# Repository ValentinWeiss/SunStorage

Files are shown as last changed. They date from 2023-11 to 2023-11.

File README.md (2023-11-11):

# SunStorage

## Installation

### Prerequisites

Install CP210x Windows Drivers: https://www.silabs.com/developers/usb-to-uart-bridge-vcp-drivers?tab=downloads

### PlatformIO
- Install the PlatformIO extension in VS Code
- Open the SunStorage project in VS Code and open the PlatformIO tab in the side menu
- Wait until PlaformIO has installed all dependencies for the SunStorage project

## Using ESP-IDF

### Tasks
Create a task for each application. To do that you have to follow the following steps:

1. Declare your application main function (choose a speaking name, not "main")
2. Add a corresponding function call of ```xTaskCreate``` to the ```app_main``` function in the file ```main.c```. The pcName can only be an array up to 16 bytes and for the stack size use a number as small as possible.<br/>
(read the Documentation for detailed information: https://docs.espressif.com/projects/esp-idf/en/latest/esp32/api-reference/system/freertos_idf.html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)
2. Only create those tasks in ```app_main``` function that you want to run continuously, because the ```app_main``` function will return when all the tasks have been created. Therefore do not use the returned handle and do not create a task with parameters there!!!

## Compiling

Compile flags can be set in the platformio.ini file.

-DTX: compile code for ESP1 (TX)

-DRX: compile code for ESP2 (RX)

## Flashing

PlatformIO: -> Press Build -> Press Upload and Monitor -> While "Connecting..." press BOOT Button then EN Button on the ESP board. https://docs.espressif.com/projects/esp-idf/en/latest/esp32/hw-reference/esp32/get-started-devkitc.html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

## Ports
If you want to reserve a port add it to the Dokumentation\Architektur\Pinout.md file.

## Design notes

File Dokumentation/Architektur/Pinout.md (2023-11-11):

## PORTS

Some of the listed ports are not available in general since they have a fixed purpose. (e.g. power supply)

# ESP 1 (TX)

GPIO 0: strange outputs during startup

GPIO 1: GPS_GPIO_TX

GPIO 2: High Power Circuit Enable

GPIO 3: GPS_GPIO_RX

GPIO 4:

GPIO 5: SD MISO

GPIO 6: Used for internal flash

GPIO 7: Used for internal flash

GPIO 8: Used for internal flash

GPIO 9: Used for internal flash

GPIO 10: Used for internal flash

GPIO 11: Used for internal flash

GPIO 12: Cell Balancing Lower Cell

GPIO 13: Coulomb Counter Discharge

GPIO 14: Cell Balancing Higher Cell

GPIO 15: DCF77 Signal

GPIO 16: UART ESP2 RX

GPIO 17: UART ESP2 TX

GPIO 18: SD MOSI

GPIO 19: SD CLK

GPIO 20: Does not exist

GPIO 21: I2C_MASTER_SDA_IO

GPIO 22: I2C_MASTER_SCL_IO

GPIO 23: SD CS

GPIO 24: Does not exist

GPIO 25: DAC USB Charger Mode 0

GPIO 26: DAC USB Charger Mode 1

GPIO 27: PWM Solar Charger

GPIO 28: Does not exist

GPIO 29: Does not exist

GPIO 30: Does not exist

GPIO 31: Does not exist

GPIO 32: ADC Battery Voltage

GPIO 33: ADC Solar Current

GPIO 34: ADC System Current

GPIO 35: ADC Battery Cell 0 Voltage

GPIO 36 (SP):

GPIO 39 (SN): ADC Coulomb

# ESP 2 (RX)

GPIO 0: strange outputs during startup

GPIO 1:

GPIO 2: Button 0

GPIO 3:

GPIO 4: Servo Rotate

GPIO 5: Servo Tilt

GPIO 6: Used for internal flash

GPIO 7: Used for internal flash

GPIO 8: Used for internal flash

GPIO 9: Used for internal flash

GPIO 10: Used for internal flash

GPIO 11: Used for internal flash

GPIO 12:

GPIO 13: LCD ON/OFF

GPIO 14:

GPIO 15: LCD D6

GPIO 16: UART ESP 1 RX

GPIO 17: UART ESP 1 TX

GPIO 18: LCD E

GPIO 19: LCD RS

GPIO 20: Does not exist

GPIO 21:

GPIO 22:

GPIO 23:

GPIO 24: Does not exist

GPIO 25: LCD D4

GPIO 26: LCD D7

GPIO 27: LCD D5

GPIO 28: Does not exist

GPIO 29: Does not exist

GPIO 30: Does not exist

GPIO 31: Does not exist

GPIO 32:

GPIO 33:

GPIO 34:

GPIO 35:

GPIO 36: Button 1

GPIO 39:

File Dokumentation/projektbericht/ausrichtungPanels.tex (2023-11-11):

\chapterauthor{Felix Wagner}
Die Ausrichtung der Solarpanele erfolgt über die vom Haupt-ESP berechneten Azimut und Elevation Werte.
Diese repräsentieren die Position der Sonne am Himmel. 
Wenn davon ausgegangen wird, dass der SunStorage Aufbau stets auf einer ebenen Fläche liegt, dann können die Azimut- und Elevationwerte direkt auf die Postionen der Rotations- und Kippservos übertragen werden. 
Somit würde sich eine direkte Ausrichtung zur Sonne ergeben und die Effektivität der Solarpanele wäre maximiert.
Dieser Fall ist jedoch im praktischen Betrieb nicht immer gegeben.

\subsubsection{Schieflage des Systems}
Steht der Aufbau schief, so ist die Trennung der Aufgabengebiete des Rotieren und Kippens der Solarpanele nicht mehr gegeben.
Somit können die Azimut und Elevation nicht mehr direkt für die Stellung der Servomotoren verwendet werden.
Kippt man etwa den kompletten Aufbau auf eine Seite, so sind die Aufgaben der Motoren komplett umgekehrt.
Für alle Orientierungen dazwischen übernehmen die Motoren Rotation und Kippen gemeinsam.

\paragraph{Beschleunigungswerte}
Um die Lage des SunStorage Systems zu ermitteln, muss die Erdbeschleunigung anhand von drei Achsen gemessen werden. 
Dies erfolgt über die Daten des Beschleunigungssensors.

\paragraph{Interpretation der Beschleunigungswerte}
Betrachtet man die Beschleunigungswerte der drei Achsen als Vektor im 3-dimensionalen Raum, 
so spannt dieser Vektor eine Ebene auf. 
Dieser Vektor muss nun an der z-Achse im Koordinatensystem gespiegelt werden. 
Damit lässt sich die physikalische Lage von SunStorage im Koordinatensystem abbilden.
Dieser Vektor wird im weiteren Verlauf $ V_{SunStorage} $ genannt.

\paragraph{Darstellen der Sonne im Koordinatensystem}
Nachdem nun SunStorage im Koordinatensystem abgebildet ist, muss die gewünschte Sonnenposition mittels eines Vektors hinzugefügt werden.
Wie bereits bekannt wird die Sonnenposition über die Werte Azimut und Elevation angegeben. 
Dabei handelt es sich um Winkel. 
Diese können mithilfe der trigonometrischen Funktionen in einem 3-dimensionalen Vektor übersetzt werden.
Hierfür wird die Berechnung in vier verschiedene Fälle aufgeteilt, welche die vier Quadranten eines 2-dimensionalen Koordinatensystems darstellen. 
\begin{itemize}
    \item I Quadrant: $x = 1 y = \tan(Azimuth)$
    \item II Quadrant: $x = -1 y = -\tan(Azimuth)$
    \item III Quadrant: $x = -1 y = -\tan(Azimuth)$
    \item IV Quadrant: $x = -\tan(Azimuth) y = -1$
\end{itemize}
Anschließend wird der Vektor aus dem Punkt (x,y) und dem Ursprung normalisiert, um mit dem später berechneten z-Wert die Sonnenposition darzustellen.\\
Die z-Koordinate wird anschließend über den Tangens des Elevationwertes bestimmt. 

$$ z = \tan(Elevation) $$

Nun stellen x, y und z den Sonnenvektor $ V_{Sonne} $ dar.\\
Ist der Elevationswinkel 90°, so wird $ V_{Sonne} $ auf (0,0,1) gesetzt, da in diesem Fall der Azimutwert vernachlässigbar ist.
Nun kann die Sonnenposition im Koordinatensystem dargestellt werden.

\paragraph{Solarpanele darstellen}
Um die Orientierung der Solarpanele im Koordinatensystem darzustellen, wird eine Ebene konstruiert, welche die Panele senkrecht in ihrer Mitte trennt.
Diese wird über die Berechnung des Orthogonalvektors der z-Achse und $ V_{SunStorage} $ bestimmt:
\[
\begin{pmatrix}
    0\\
    0\\
    1\\
\end{pmatrix}
\times
V_{SunStorage}
=
V_{ortho}
\]
Aus dem Vektor $ V_{ortho} $ lässt sich die Koordinatenform als Ebene erstellen.
\[V_{ortho}x \cdot x + V_{ortho}y \cdot y + V_{ortho}z \cdot z = 0\] 
Nun kann diese Ebene um die Achse von $ V_{SunStorage} $ rotiert werden.
Dies wird über die allgemeine Drehmatrix umgesetzt.
\[
R_n(\alpha)
=
\begin{pmatrix}
    n^2_1(1-\cos\alpha)+\cos\alpha & n_1n_2(1-\cos \alpha)-n_3\sin\alpha & n_1n_3(1-\cos\alpha)+n_2\sin\alpha\\
    n_2n_1(1-\cos\alpha)+n_3\sin\alpha & n^2_2(1-\cos\alpha)+\cos\alpha & n_2n_3(1-\cos\alpha)-n_1\sin\alpha\\
    n_3n_1(1-\cos\alpha)-n_2\sin\alpha & n_3n_2(1-\cos\alpha)+n_1\sin\alpha & n^2_3(1-\cos\alpha)+\cos\alpha\\
\end{pmatrix}    
\]
An Stelle von $ n = (n_1, n_2, n_3)^T $ wird $ V_{SunStorage}^T $ eingesetzt.
Dies entspricht der Bewegung des Rotationsservomotors.
Anschließend kann die Rotation der Ebene gesucht werden, für die $ V_{Sonne} $ eingesetzt
in  die Koordinatenform der Ebene des Normalenvektors $ V_{ortho} $ den geringsten Wert hat. %TODO der satz doof
Damit ist die Bestimmung der Stellung des Rotationsmotors beendet, da dies bedeutet, 
dass $ V_{Sonne} $ in der Ebene von  $ V_{ortho} $ liegt.
Anschließend erfolgt die Berechnung der Stellung des Kippmotors.
Dafür wird ein weiterer Orthogonalvektor $ V_{opt} $ erzeugt. 
Dieser liegt zwischen der z-Achse und $ V_{ortho} $. 
Die Stellung des Kippmotors kann somit durch die Berechnung des Winkels zwischen $ V_{opt} $ und $ V_{Sonne} $ bestimmt werden:
\[\alpha = \arccos(\frac{V_{opt} \cdot V_{Sonne}}{\left| V_{opt} \right| \cdot \left| V_{Sonne} \right|})\]

\subsubsection{Schieflage des Kompass}
Der Kompass liefert in Abhängigkeit seiner Ausrichtung unterschiedliche Werte.
In diesem Kapitel wird die notwendige Korrektur beschrieben.
\paragraph{Nordausrichtung}
\chapterauthor{Felix Wagner}
Die Bestimmung der Orientierung zu Norden erfolgt über die Winkelberechnung zwischen der 
y-Achse und der Geraden des Koordinatenursprungs und des aktuellen (x, y)-Messpunkts. 
Dieser Winkel wird mittels der Tangensfunktion ermittelt. Siehe Abbildung \autoref{fig:circlecenter}.
Die C Standardbibiliothek $math.h$ liefert hierfür die Funktion $atan2f$, 
welche den Winkel als float Datentyp zurückgibt 
und die vier verschiedenen Quadranten des Koordinatensystems berücksichtigt.

\paragraph{Schieflagenkorrektur}
\chapterauthor{Felix Wagner}
Es ist nicht immer gegeben, dass der Kompass perfekt gerade liegt. 
Deshalb müssen die Sensorwerte unter Berücksichtigung des vom Beschleunigungssensor 
gestelltem Orientierungsvektor angepasst werden. 
Dies erfolgt über die sogenannte Vektorprojektion. 
Dabei wird über folgende Formel \[\vec{a_{projected}} = \frac{\vec{a} \circ \vec{b}}{\vec{b} \circ \vec{b}} \cdot \vec{b} \]
der Vektor aus den Kompasswerten auf die Orientierung des Vektors der Beschleunigungswerte projeziert. 
Anschließend werden die x- und y-Werte des projezierten Vektors von denen des Kompassvektors subtrahiert. 
Somit sind die Kompasswerte bereit für die oben besprochene Weiterverarbeitung.

\subsubsection{Verbesserter Algorithmus}
Der implementierte Algorithmus nutzt für seine Berechnung viele Multiplikationen und trigonometrische Funktionen.
Dies erzeugt einen großen Rechenaufwand und ist im Dauerbetrieb nicht optimal.
Dies wirkt sich aufgrund der großen zeitlichen Abstände der Funktionsaufrufe kaum negativ auf die Funktionsweise von SunStorage aus.
Im Folgenden wird eine effizientere Formel erklärt.\\
Die Berechnung von $ V_{SunStorage} $  und $ V_{Sonne} $ erfolgt analog zum ursprünglichen Algorithmus.
Anstatt einer Ebene für die Solarpanele eine Ebene über den Vektor $ V_{SunStorage} $ in Koordinatenform erzeugt.
\[V_{SunStorage}x \cdot x + V_{SunStorage}y \cdot y + V_{SunStorage}z \cdot z = 0\] 
Anschließend wird die Spitze von $ V_{Sonne} $ als Ausgangspunkt für eine Gerade $ G_{Sonne} $ mit dem Richtungsvektor $ V_{SunStorage} $ generiert.
Der Schnittpunkt von $ G_{Sonne} $ mit der Ebene von SunStorage stellt mit dem Ursprung des Koordinatensystems den Vektor $ V_{opt} $ dar.
Aus $ V_{opt} $ kann wiederum die Stellung für Rotation und Kippen der Motoren analog zum vorherigen Ansatz berechnet werden.

\subsubsection{Bestimmung der Abweichung zum Norden}
\chapterauthor{Felix Wagner}
Die Bestimmung der Orientierung zu Norden erfolgt über die Winkelberechnung zwischen der 
y-Achse, der Geraden des Koordinatenursprungs und des aktuellen (x, y)-Messpunkts. 
Dieser Winkel wird mittels der Tangensfunktion ermittelt. (siehe \autoref{fig:circlecenter})
Die C Standardbibliothek $math.h$ liefert hierfür die Funktion $atan2f$, 
welche den Winkel als float Datentyp zurückgibt und dabei die vier verschiedenen Quadranten des Koordinatensystems berücksichtigt.

\paragraph{Schieflagenkorrektur}
Es ist nicht immer gegeben, dass der Kompass perfekt gerade liegt. 
Deshalb müssen die Sensorwerte unter Berücksichtigung des Orientierungsvektors, die der Beschleunigungssensor liefert, angepasst werden. 
Dies erfolgt über eine Vektorprojektion.
Mithilfe der folgenden Formel wird der Vektor aus den Kompasswerten auf die Orientierung des Vektors der Beschleunigungswerte projiziert.
\[\vec{a_{projected}} = \frac{\vec{a} \circ \vec{b}}{\vec{b} \circ \vec{b}} \cdot \vec{b} \]
 
Anschließend werden die x- und y-Werte des projizierten Vektors von den Werten des Kompassvektors subtrahiert. 
Somit sind die Kompasswerte bereit für die in Weiterverarbeitung. \autocite{compasstilt}

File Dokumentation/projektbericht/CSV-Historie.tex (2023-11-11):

\subsubsection{CSV-Historie}\label{csvhistory}
\chapterauthor{Johannes Treske}
Eine Historie der Messdaten wird benötigt, um eine grafische Darstellung über die Zeit, im Web-Frontend darzustellen.
Ursprünglich war geplant, eine SQLite Datenbank zu verwenden.
Diese sollte auf der SD-Karte gespeichert werden.
Es gibt jedoch nur SQLite Bibliotheken, die mit älteren Versionen von ESP-IDF kompatibel sind, welche aber von unserem Modell des ESP32 nicht unterstützt werden.
Deswegen nutzen wir CSV-Dateien zum Speichern der Messdaten.

Für jeden Tag wird eine eigene CSV-Datei verwendet, die nach einem Teil des Timestamps benannt wird (YYYYMMDD.csv).
Innerhalb einer Datei besteht eine Zeile immer aus einer Reihe an Messdaten, eindeutig bestimmbar durch den Timestamp und getrennt durch Kommas.
Eine Zeile besteht aus allen Messwerten, die im Datenbankmodell in \autoref{fig. Datenbankmodell} zu sehen sind.
Um eine einfache Interaktion mit der Datenbank zu ermöglichen, wurde das Datenbankinterface geschrieben.
Die zwei wichtigsten Funktionen ermöglichen das Schreiben eines Messdatensets bzw. das Auslesen von Messdaten.

\begin{lstlisting}[language=C]
esp_err_t dbStoreReadings(readings_data_set_t readings);
esp_err_t dbGetReadings(readings_read_config_t config, cJSON** jsonOut);
\end{lstlisting}

Die Funktionsdeklaration der Lese-Funktion zeigt, dass ein JSON-Objekt zurückgegeben wird.
Dieses Objekt besteht aus einem JSON-Array, der alle Messdaten der gewünschten Zeitspanne, in Sets zusammengefasst, enthält.
Das JSON-Objekt kann so direkt an das Web-Frontend weitergegeben werden.
Über den \textit{config} Parameter kann eingestellt werden, welcher Zeitbereich abgefragt werden soll und welche Spalten/Messdaten benötigt werden.

Bei allen Funktionen des Datenbankinterfaces muss stets darauf geachtet werden, dass nicht mehrere Tasks auf die gleiche Datei zugreifen können.
Dieses Problem wird durch das Verwenden von Mutexen gelöst.
Weitere Funktionen, die das Datenbankinterface bereitstellt, sind Funktionen zum Initialisieren bzw. Deinitialisieren, sowie Funktionen, mit denen Daten gelöscht werden können.

\begin{figure}
    \centering
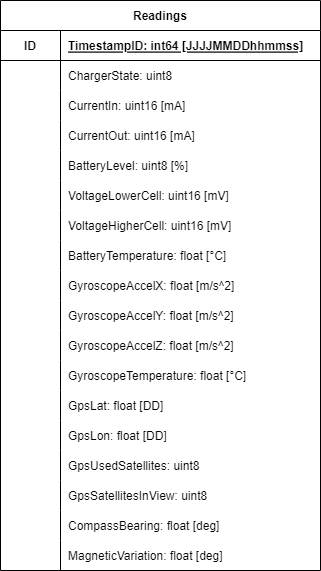
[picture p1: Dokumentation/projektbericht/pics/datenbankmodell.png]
    
    \caption{Datenbankmodell}
    \label{fig. Datenbankmodell}
\end{figure}

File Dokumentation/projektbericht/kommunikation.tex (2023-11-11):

\subsection{Kommunikation}
\chapterauthor{Philipp Thaler}
Um es dem Benutzer zu ermöglichen mit dem System zu interagieren, benötigt das System funktionale Schnittstellen, um mit der außenwelt zu kommunizieren.

Außerdem wird ein Kommunikationsweg zwischen den beiden ESP32 Boards, die zur Steuerung des Systems verwendet werden, benötigt.
Die folgenden Kapitel geben einen Einblick wie das System intern und nach außen kommuniziert.
%Philipp

\subsubsection{SD-Karten Modul}
\chapterauthor{Philipp Thaler}
Mit Hilfe des SD-Karten Moduls von AZ-Delivery kann das System auf eine SD-Karte zugreifen und auf dieser Dateien ablegen, lesen oder auch löschen.
ESP-IDF bietet zwei grundsätzliche Wege wie ein SD-Karten Modul eingebunden werden kann, wie den SDMMC Treiber und den SD SPI Treiber. Da das Modul von AZ-Delivery via SPI angesteuert werden muss, wird für die Einbindung in das System der SD SPI Treiber verwendet.

Um den Treiber zu initialisieren, wird zunächst eine Konfiguration angelegt. Diese beinhaltet die maximale Dateianzahl, die aktuell auf fünf gestellt ist und ob die SD-Karte bei gescheitertem Mountversuch formatiert werden soll oder nicht.
Da keine Formatierung erfolgen soll, ist diese Funktion deaktiviert.

Der Bus, über den kommuniziert wird, muss ebenfalls initialisiert werden. Hier werden die PINs in der Konfiguration gesetzt mit denen das SD-Karten Modul an das ESP32 angeschlossen ist.
Anschließend wird der SPI Bus mit der erstellten Konfiguration initialisiert. Wichtig ist anzumerken, dass der Pullup Widerstand am ESP32 Port, an dem der CS PIN des SD-Karten Moduls angesteckt ist, eingeschalten wird. Sonst ist ein mounten des Dateisystems nicht möglich.
Wenn diese Einstellungen ohne Fehler ausgeführt werden, wird das Dateisystem von der SD-Karte auf das in der global definierten \glqq SDC\_MOUNT\_POINT\grqq{} Variable gemountet und ist somit für das gesamte System verfügbar.

Um Dateien lesen oder schreiben zu können, werden die Befehle \glqq fopen()\grqq{}, \glqq fprintf()\grqq{} und \glqq fclose()\grqq{} verwendet. Diese ermöglichen das öffnen und beschreiben der gewünschten Dateien. Hierfür stellt der \glqq sdCardService\grqq{} eine extra Funktion \glqq sdCardWriteFile()\grqq{} bereit.
Der Funktion kann der gesamte Pfad einer Datei und der Inhalt übergeben werden. Das Beschreiben und Speichern der Datei übernimmt die Funktion selbst.

Die SD-Karte stellt ein wichtiges Glied im Projekt dar, da dort sowohl die Datenbank als auch der Systemstatus regelmäßig Dateien ablegen oder aktualisieren.

%Philipp

\subsubsection{Wi-Fi}
\chapterauthor{Philipp Thaler}
Eine Schnittstelle nach außen bietet der bereits verbaute WLAN Chip auf dem ESP32 Board. Das ESP-IDF Framework stellt drei Modi zur Verfügung in denen das WLAN Modul betrieben werden kann.

Das System startet und überprüft zunächst ob eine \glqq wifi.txt\grqq{} auf der SD-Karte vorhanden ist. Ist diese vorhanden, wird das JSON der Datei ausgelesen und die SSID und das Passwort gelesen.
Diese beiden Werte werden verwendet, damit sich das ESP32 mit der SSID verbindet. Das Board ist dann im Station Modus (STA).

Ist keine \glqq wifi.txt\grqq{} vorhanden oder sind die Einträge in der Datei fehlerhaft, startet das System im Access Point Station Modus (APSTA). Dieser Modus ist eine Mischung aus Access Point und Station Modus.
Es bietet dem ESP32 die Möglichkeit nach verfügbaren WLAN Netzwerken zu scannen, aber gleichzeitig ein eigenes WLAN Netzwerk zu erstellen und Verbindungen entgegenzunehmen.

Der APSTA Modus ist der Fallback Modus. In dieser Einstellung können sich bis zu fünf Geräte mit dem SunStorage WLAN verbinden. Die SSID ist auf \glqq SunStorage\grqq{} eingestellt und das Passwort \glqq sunstorage123\grqq{} wird standardmäßig verwendet.
Diese Einstellung ist nur zum initialisieren und nicht als Dauerbetrieb gedacht. Nachdem sich der Benutzer verbunden hat kann sich Dieser über die Weboberfläche, die mit der IP-Adresse 192.168.1.1 angesprochen wird, mit dem System verbinden und das SunStorage und die WLAN Konfiguration bearbeiten.

Die Standardwerte sind im Quellcode hinterlegt. Somit kann im Notfall immer auf das System zugeriffen werden, da sich das System nach spätestens fünf Verbindungsabbrüchen automatsich in den APSTA Modus versetzt.

Ist das System hingegen erfolgreich mit dem Heimnetz verbunden, lässt es sich via selbsteigestelltem DNS oder IP-Adresse, die dem Gerät vom Heimnetz-DHCP zugewiesen wird, erreichen.
%Philipp

\subsubsection{HTTP Server}
\chapterauthor{Philipp Thaler}
Der HTTP-Server ist für das Ausliefern der Webseite Dateien zuständig und liefert auch über definierte URL Aufrufe Daten an das Frontend. Zunächst wird der HTTP-Server mit Standardkonfigurationsparametern erstellt.
Diese werden erweitert, damit bis zu 20 HTTP-Handler verwendet werden können. Danach wird der HTTP Server initialisiert und gestartet. Wenn der Dienst startet, werden die insgesamt neun HTTP Handler einzeln geladen.

Der HTTP-Server ist generell über die Standard-URL \glqq /api/v1/\grqq{} für API Aufrufe erreichbar. Um auf spezifische Funktionen zuzugreifen, erweitert das Frontend die URL und erstellt dafür eine HTTP-Anfrage.
Am Server wird diese Anfrage verarbeitet und die entsprechenden internen Funktionen aufgerufen. Nach dem erfolgreichen Sammeln der Informationen für die Anfrage, erstellt der Server ein JSON-Objekt und sendet diese zurück an das Frontend.

Der HTTP-Service muss nicht wie andere Funktionen in einen extra Task geschrieben werden, da FreeRTOS diese Funktionalität bereits mit dem Initialisieren bietet.
Generell sendet der HTTP-Server bei auftretenden Fehlern ein HTTP-Statuscode 500 \glqq Internal Server Error\grqq{}. Bei erfolgreicher Ausführung wird der HTTP-Statuscode 200 \glqq OK\grqq{} verschickt.

Nachfolgend wird auf die neun HTTP-Handler eingegangen und deren Funktionsweise erklärt:

\subparagraph{shutdownHandler} Der erste HTTP-Handler hat laut Spezifikation die Aufgabe, einzelne Bausteine wie das DCF77 Modul, das GPS Modul, die HTTP Funktionalität oder das WiFi für eine vom Nutzer gewählte Zeit abzuschalten.
Dafür sendet das Frontend eine HTTP-POST-Anfrage auf die URL \glqq /api/v1/shutdown\grqq{}.

Im Body wird angegeben welche Module ausgeschaltet werden. Der Handler prüft nun, welchen der Services er für wie viele Sekunden abschalten muss.
Dazu wird der als JSON-String übergebene Body in ein cJSON Objekt umgewandelt um daraus die nötigen Werte extrahiert.

Danach werden die entsprechenden \glqq Stop-Tasks\grqq{} erstellt, die vom FreeRTOS ausgeführt werden.
Diese Tasks schalten die einzelnen Module aus und nach den angegebenen Sekunden wieder ein. Nach Erstellung der Tasks, wird dem Client eine Antwort gesendet. Diese enthält den HTTP Statuscode 200.

Somit weiß der Client, dass die Anfrage richtig bearbeitet wird.
Sollten während dem Erstellen oder Abschalten der Module Fehler auftreten, wird eine Fehlermeldung an das Frontend übergeben.

\subparagraph{systemStatus-Handler} Die Systeminformation URL \glqq /api/v1/system\grqq{} wird über eine GET-Anfrage vom Client aufgerufen.
Der Handler gibt generelle Informationen über das verwendete ESP32 zurück.
Der Handler fügt alle Informationen, die über globale Variablen vom FreeRTOS zur Verfügung gestellt werden, in ein JSON Objekt zusammen und übergiebt dieses an das Frontend.

Das JSON Objekt beinhaltet die Versionsnummer des Boards, die Anzahl der CPU-Kerne, das Modell, die Features die das ESP besitzt, den freien und belegten Heap-Speicher und die MAC-Adresse.

\subparagraph{wifiAPListHandler} Dem Nutzer wird eine Liste aller verfügbaren SSIDs in der Umgebung angezeigt. Dafür ist der \glqq wifiAPListHandler\grqq{} zuständig. Dieser wird mit einer HTTP-GET Anfrage auf die URL \glqq /api/v1/wifi/list\grqq{} aufgerufen.
Diese Funktion ruft die \glqq wifiScan\grqq{} Methode auf. Sie befindet sich in der \glqq wifiService.c\grqq{} Datei. Das Framework FreeRTOS bietet eine Funktion, die es ermöglicht alle SSIDs zu ermitteln, mit der sich das ESP verbinden kann.

Nach erfolgreicher Ausführung dieser Funktion wird für jeden gefundenen Access Point, dessen Informationen in ein JSON Objekt geschrieben. Dieses JSON Objekt wird dann an ein zuvor erstelltes übergeordnetes JSON Objekt angehängt.
Nun befinden sich alle Informationen in einem großen Objekt, welches nun an den Client gesendet werden kann.

\subparagraph{wifiConfigureHandler} Nachdem der Nutzer bereits eine Anzeige von verfügbaren Zugangspunkten hat, ist der Nutzer in der Lage, das ESP32 damit zu verbinden.
Diese Funktionalität bietet der \glqq wifiConfigureHandler\grqq{}. Der Client kann mittels einer HTTP-POST Anfrage auf die URL \glqq /api/v1/wifi/configure\grqq{} dem System mitteilen, mit welcher SSID und mit welchem Passwort sich verbunden werden soll.

Aus dem übermittelten HTTP-Body extrahiert der Handler die SSID und das Passwort.
Die beiden Werte werden in die \glqq wifi.txt\grqq{} Datei geschrieben, um danach das Wi-Fi Modul neu zu initialisieren.

Deswegen wird die \glqq initWifi\grqq{} Methode angepasst, damit diese auch eine Neuinitialisierung während des Systembetriebs durchführen kann.

Sie liest die entweder neu geschriebene oder aktualisierte \glqq wifi.txt\grqq{} Datei ein und versucht eine Verbindung mit der dort hinterlegten SSID aufzubauen.
Sollten während des Vorgangs Fehler entstehen, wird die Neuinitialisierung des WLAN Moduls abgebrochen und der Client bekommt eine Fehlermeldung als Antwort.

Wenn der Handler die Konfiguration ohne Fehler durchführt, muss sich der Benutzer erst wieder mit dem richtigen WLAN verbinden, um eine Kommunikation mit dem ESP herzustellen, da dieses nun mit einem anderen WLAN Access Point verbunden ist.

\subparagraph{stateSetterHandler} Um dem Benutzer Einsicht in das System zu geben und welche internen Werte das SunStorage gerade verarbeitet, bietet der HTTP-Server einen Endpunkt für GET Anfragen unter der URL \glqq /api/v1/state\grqq{} an.

Hier kann das Frontend alle aktuellen Systemvariablen abholen. Dazu klont der HTTP-Handler den aktuellen Systemstatus. Dieser Status wird von einem JSON Objekt in einen String umgewandelt und an das Frontend gesendet.

Diese URL erweist sich als hilfreiche Debugging-Möglichkeit, da es sonst nicht möglich ist den aktuellen Systemzustand einzusehen.

\subparagraph{stateGetterHandler} Es ist möglich den Systemzustand für gewisse Bereiche anzupassen. Deswegen bietet der HTTP-Server unter der gleichen URL wie beim Auslesen des Systemstatus diese Funktionalität an. Nur muss hierfür die HTTP-POST-Methode verwendet werden.
Über die Schaltflächen auf der Webseite ist es dem Benutzer möglich, die Werte auf die eigenen Bedürfnisse anzupassen. Sobald das Frontend die Anfrage absendet, liest der \glqq stateSetterHandler\grqq{} den übergebenen JSON-String aus und wandelt diesen wieder in ein JSON Objekt um.

Nun wird für jeden änderbaren Wert geprüft, ob dieser im HTTP-Body enthalten ist. Wird dieser Wert nicht gesendet, erfolgt auch kein setzten im Systemstattus.
Ist ein veränderbarer Wert als JSON-Key gesetzt, wird der zugehörige JSON-Value ausgelesen und die entsprechende Setter-Funktion im Systemstatus aufgerufen.

Nach erfolgreicher Verarbeitung, sendet der Server den HTTP-Statuscode 200.

\subparagraph{databaseGetHandler} Die historischen Daten für das Frontend stellt die Funktion databaseGetHandler unter der URL \glqq /api/v1/database\grqq{} mit der HTTP-POST Methode zur Verfügung. Es wird absichtlich die POST-Methode verwendet, da der Client einen Start- und Endzeitpunkt an den Server übergeben muss um nicht zu viele Daten aus der Datenbank zu filtern.

Filtert der Client zu viele Daten aus der Datenbank, kommt es zu einer sehr großen Last auf dem Microkontroller. Der Client kann auch angeben, welche Daten er aus der Datenbank extrahieren möchte.

Dies geschieht mit simplen TRUE/FALSE Werten für die zu extrahierenden Werte. Das genaue Vorgehen wird in \autoref{csvhistory} erläutert. Nachdem die Datenbank das JSON-Objekt erstellt hat, kann der HTTP-Server diese in einen String konvertieren und an den Client senden.

\subparagraph{recalibrateBatteryHandler} Die Batterie Rekalibrierungsfunktion ist unter der URL \glqq /api/v1/battery/calibrate\grqq{} mit der HTTP-GET Methode erreichbar. Der \glqq recalibrateBatteryHandler\grqq{} ruft die bereitgestellte Rekalibrierungsfunktion des Chargers auf.
Dem Client wird nach der Ausführung eine HTTP-Status Meldung mit Code 200 gesendet. Die Anfrage ist somit erfolgreich.

\subparagraph{commonGetHandler} Um die statischen Dateien der Webseite an den Client ausliefern zu können, benötigt der HTTP-Server noch eine default URL. Diese ist wie folgt angegeben \glqq /*\grqq{}. Sollte keiner der oben genannten Handler mit der URL ausgelöst werden, übernimmt der \glqq commonGetHandler\grqq{} alle HTTP-GET Anfragen.
Dieser ist so konzipiert, dass ein Aufruf auf die Root-URL immer die index.html Datei ausliefert. Für alle anderen URL Pfade versucht der Server die entsprechende Datei im SPIFFS zu finden und auszuliefern.

Soll nun die index.html ausgeliefert werden, so überprüft der Server zunächst ob die Datei auslieferbar ist. Hier prüft der Server auf bestimmte Dateiendungen, wie zum Beispiel .html, .png oder .css. Sollte die Datei nicht in der Liste stehen, liefert der Server eine Fehlermeldung an den Client.

Danach prüft das System, ob die Datei auch im Dateisystem existiert. Auch hier gibt der Server eine Fehlermeldung, sollte die Datei nicht vorhanden sein. Der Server setzt den Dateityp im HTTP-Protokoll-Header, da der Browser am Client wissen muss welchen Dateityp er empfängt.

Beim Erstellen des SPI-Dateisystems ist aufgefallen, dass die Artefakte der Webseite größer als die 4MB Flashspeicher sind. Deswegen werden die Frontend Dateien mit dem Programm \glqq gzip\grqq{} komprimiert.

Für die vorher komprimierten Java-Script Dateien muss der Server das HTML-Header-Flag \glqq gzipEncoding\grqq{} setzen. Nur damit ist der Browser in der Lage, die Dateien nach dem Empfangen zu entpacken und dem Nutzter darzustellen.

Da nun alle notwendigen HTTP-Header gesetzt sind, liest der Server die Datei in einen Buffer ein und überträgt diesen mit der vom Framework bereitgestellten Funktion zur Übertragung von Buffern.

So kann eine große Datei in kleinen Stücken eingelesen und gesendet werden, ohne den Arbeitsspeicher und den Prozessor des Mikrokontrollers zu sehr zu belasten.
Ist die Datei vollständig übertragen wird, dem Browser ein leerer Inhalt gesendet um ihm zu signalisieren, dass die Dateiübertragung abgeschlossen ist.
%Philipp

\subsubsection{Sender-Empfänger Setup}
\chapterauthor{Philipp Thaler und Johannes Treske}

Das Zusammenbringen und Integrieren der einzelnen Module hat gezeigt, dass die physischen Ports des ESP32 nicht ausreichen um alle Sensoren und Aktoren zu verbinden.
Deswegen musste eine Ausweichlösung gefunden werden.
Diese Lösung ist ein zweiter ESP32, der Daten vom Controller ESP empfängt und mit diesen Daten arbeitet.
Die Steuerung des gesamten Systems erfolgt nun nicht mehr über einen ESP, sondern über ein Verbund aus Controller ESP und peripherem ESP.
Dadurch ist es möglich, dass die Motorsteuerung und das Display von dem peripheren ESP gesteuert werden.

Die Kommunikation zwischen den beiden Mikrocontrollern wird mit dem UART Protokoll realisiert. Hierzu werden jeweils zwei Ports für das Senden und Empfangen auf den beiden Boards definiert.

Der Controller ESP soll nur in bestimmten Zeitintervallen den aktuellen Systemzustand an den periphere ESP senden, um die CPU Auslastung zu minimieren.
Deswegen ist der Sendevorgang in den Task eingebaut, der den Systemzustand in gleichmäßigen Intervallen auf die SD-Karte schreibt.
Außerdem wird der Systemzustand nur dann gesendet, wenn auch eine Veränderung stattgefunden hat.
Dies ist nur möglich, da der zweite ESP keine zeitkritischen Berechnungen ausführt.

Der Sender klont das JSON Objekt des Systemzustandes zur Übertragung.
Danach wird das JSON Objekt in eine Zeichenkette ohne Zeilenumbrüche umgewandelt und dessen Länge bestimmt.
Anschließend wird die Zeichenkette unter Angabe der Länge mithilfe der UART Sendefunktion des ESP-IDF Frameworks gesendet.
Da der Sendevorgang in dem Task zum persistenten Speichern des Systemzustandes aufgerufen wird, muss kein extra Sendetask erstellt werden.

Der Empfänger hingegen führt in kurzen Zeitintervallen den UART Empfangstask aus. Hier ist es notwendig einen eigenen Task anzulegen damit das Empfangen immer wieder neu planmäßig ausgeführt werden kann.
Nachdem die Funktion die Länge der Daten ermittelt hat, liest die Empfangsfunktion die Zeichenkette in den Buffer des Empfängers. Sobald ein \glqq \textbackslash n\grqq{} in der übertragenen Zeichenkette erkannt wird, weiß der Empfänger, dass die Übertragung komplett ist.
Nun wird die Zeichenkette mithilfe der cJOSN-Bibliothek in ein JSON-Objekt umgewandelt und der Systemstatus anhand des erstellen Objektes gesetzt.
Der periphere ESP32 ist dann in der Lage, die Motoren und das Display mit den nötigen Informationen aus dem Systemstatus anzusteuern.

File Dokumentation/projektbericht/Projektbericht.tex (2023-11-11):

\documentclass[12pt,a4paper,bibliography=totocnumbered,listof=totocnumbered]{article}
% packages:
\usepackage{float}
\usepackage[ngerman]{babel}
%\RequirePackage[nottoc,numbib]{tocbibind}
\RequirePackage[hidelinks]{hyperref}
\RequirePackage[utf8]{inputenc}
\RequirePackage{pdfpages}
\usepackage[backend=biber, style=ieee, isbn=false, doi=false, url=false,block=space,pagetracker=true, backref=true]{biblatex}
\usepackage{titlesec}
\usepackage{makecell}
\usepackage{textgreek}
\usepackage{multirow}
\usepackage{ltablex}

\bibliography{quellen.bib}
\input{lib/includes.tex}
\input{lib/commands.tex}

\setcounter{secnumdepth}{4}
\titleformat{\paragraph}
{\normalfont\normalsize\bfseries}{\theparagraph}{1em}{}
\titlespacing*{\paragraph}
{0pt}{3.25ex plus 1ex minus .2ex}{1.5ex plus .2ex}

\makeatletter
\newcommand{\chapterauthor}[1]{%
  {\parindent0pt\vspace*{-5pt}%
  \linespread{1.1}\small\scshape#1%
  \par\nobreak\vspace*{3pt}}
  \@afterheading%
}
\makeatother

\begin{document}
\pagenumbering{gobble}
----------------------------------------------------------------------------------------------------------
% Titelseite
% ----------------------------------------------------------------------------------------------------------
\MyTitlepage[pics/logo.png]{6}{
    \texttt{lukas.eigenstetter@st.oth-regensburg.de}\\
	\texttt{philipp.thaler@st.oth-regensburg.de}\\    
    \texttt{johannes.treske@st.oth-regensburg.de}\\    
    \texttt{matthias.unterrainer@st.oth-regensburg.de}\\
    \texttt{felix.wagner@st.oth-regensburg.de}\\
    \texttt{valentin.weiss@st.oth-regensburg.de}}

\cleardoublepage
% ----------------------------------------------------------------------------------------------------------
% Inhaltsverzeichnis
% ----------------------------------------------------------------------------------------------------------
\pagenumbering{Roman}
\tableofcontents
\pagebreak
\pagenumbering{arabic}

% ----------------------------------------------------------------------------------------------------------
% Inhalt
% ----------------------------------------------------------------------------------------------------------
% Abstände Überschrift
%\titlespacing{\section}{0pt}{12pt plus 4pt minus 2pt}{6pt plus 2pt minus 2pt}
%\titlespacing{\subsection}{0pt}{12pt plus 4pt minus 2pt}{4pt plus 2pt minus 2pt}
%\titlespacing{\subsubsection}{0pt}{12pt plus 4pt minus 2pt}{2pt plus 2pt minus 2pt}

% Kopfzeile
\renewcommand{\sectionmark}[1]{\markright{#1}}
\renewcommand{\subsectionmark}[1]{}
\renewcommand{\subsubsectionmark}[1]{}
\lhead{Kapitel \thesection}
\rhead{\rightmark}

\onehalfspacing
\renewcommand{\thesection}{\arabic{section}}
\renewcommand{\theHsection}{\arabic{section}}
\setcounter{section}{0}

\newpage
% ----------------------------------------------------------------------------------
% Kapitel: Allgemeine Informationen
% ----------------------------------------------------------------------------------
\section{Stundenlisten}
In diesem Kapitel sind die Stundenlisten der Gruppenmitglieder in alphabetischer Reihenfolge aufgelistet.
Woche 1 ist jeweils die Woche, die am 20. März 2023 beginnt.
Woche 14 bis 17 fallen in den Zeitraum nach der Abschlusspräsentation.
Sie werden daher in einem gemeinsamen Abschnitt zusammengefasst.

\newpage
\subsection{Lukas Eigenstetter}
\input{Stundenlisten/LukasEigenstetter.tex}

\subsection{Philipp Thaler}
\input{Stundenlisten/PhilippThaler.tex}

\subsection{Johannes Treske}
\input{Stundenlisten/JohannesTreske.tex}

\subsection{Matthias Unterrainer}
\input{Stundenlisten/MatthiasUnterrainer.tex}

\subsection{Felix Wagner}
\input{Stundenlisten/FelixWagner.tex}

\subsection{Valentin Weiß}
\input{Stundenlisten/ValentinWeiss.tex}

\section{Dokumentation}\label{Dokumentation}
\chapterauthor{Felix Wagner}
SunStorage ist ein gemeinschaftliches Projekt, welches im Rahmen der Vorlesung \glqq Datenverarbeitung in der Technik\grqq \ druchgeführt wurde.
Ziel dieser Vorlesung ist die Planung, Dokumentation, Implementierung und Testen eines Projektes aus dem Bereich der Technischen Informatik durchzuführen. 
Wichtig hierbei ist auch das Erlernen von Teamfähigkeiten, um mit seinen Kommilitonen effektiv zusammenarbeiten zu können.\\
Nach der Projektsuche hat sich das Team letztendlich für das Projekt SunStorage entschieden.
Gerade in Zeiten großer Strompreiserhöhungen ist es für viele Bürger wichtig, eine autonome Stromversorgung sicherzustellen. 
In den vergangenen Jahren gab es große Fortschritte in den Bereichen Photovoltaik und Speichertechnologie. 
Viele Haushalte besitzen bereits eine Kombination dieser Technologien in Form einer Photovoltaikanlage mit Batteriespeicher und in industriellen Anlagen können die Panele optimal der Sonne ausgerichtet werden.
Für tragbare Geräte gibt es teilweise auch bereits derartige Produkte. 
Diese sind aber wenig effizient, da sich diese nicht selbst in einen optimalen Winkel 
zur Sonne ausrichten können, und nur selten vernetzbar sind.\\
Ziel von SunStorage ist es, die Stromspeicherung, eine optimale Sonnenausrichtung und die Vernetzung in das Heimenetz in einem mobilen System zu vereinen, um damit verschiedene USB-Verbraucher betrieben zu können.

\subsection{Projektüberblick}
\chapterauthor{Felix Wagner}
Nun wird auf die einzelnen Komponenten des SunStorage-Systems und deren Zusammenspiel eingegangen.\\
Der hölzerne Grundaufbau vereint die Elektronikplattform mit der Ausrichtungsmechanik der Solarpanele. 
Somit kann das Gesamtsystem schnell an andere Orte verlegt werden.\\
Auf der Elektronikplattform ist unter anderem ein Batterie Management System verbaut, welches mit dem produzierten Strom
der Solarpanele die Lithium Polymer Akkus läd. Diese Akkus stellen anschließend den Strom für die restlichen
Komponenten zur Verfügung und werden durch einen Temperatursensor überwacht.\\
Um den Konfigurationsaufwand für den Nutzer gering zu halten, sind viele verschiedene Sensoren nötig.
Ein GPS-Modul stellt dabei hierbei die für die Berechnung der Sonnenposition wichtigen Standortkoordinaten,
sowie Informationen über die magnetische Varianz zum Nordpol und einen Zeitstempel mit Datum und Uhrzeit bereit.
Das Kompassmodul gibt die Ausrichtung in die nördliche Himmelsrichtung wieder und der Beschleunigungssensor
erkennt mögliche Schieflagen des SunStorage-Systems. Durch all diese Sensoren ist es nach einem Positionswechsel
des Aufbau nicht nötig dem System Informationen über den neuen Standort mitzuteilen.\\

\input{mechanischerAufbau.tex}

\subsubsection{Halterung für Hardware}
\chapterauthor{Lukas Eigenstetter}
Die Sensoren, Platinen und Module sind auf einer Holzplatte montiert.
Diese stammen aus Resten im Labor.
Alle Module, die Befestigungslöcher besitzen, wurden mithilfe von Schrauben fixiert.
In die Platinen für Neben-ESP, Haupt-ESP und Displaysteuerung wurden zu diesem  Zweck größere Löcher gebohrt.
Da die Löcher des DCF-77 Moduls sehr klein sind, wurde es mithilfe von isolierten Drähten festgeklemmt.
Diese wurden auf der Unterseite des Bretts festgeklebt und durch Löcher nach oben geführt.
Lediglich der Kompasssensor und die USB-Ladeschnittstelle wurden direkt mit Heißkleber befestigt.
Um trotz überstehender Schrauben einen geraden und festen Stand zu garantieren, wurden links und rechts auf der Unterseite Latten festgeklebt.

\begin{figure}[htpb]
    \centering
    
    \caption{Aufbau der Module und Sensoren auf der Holzplatte}\label{brett}
\end{figure}

\autoref{brett} zeigt den Aufbau auf dem Brett.
Der Temperatursensor ist nicht sichtbar, da er unter den Akkus liegt.
Das Akkufach wurde durch zwei Schrauben und einen Klettverschluss realisiert.
Die Schrauben sorgen dafür, dass der Akku nicht nach vorne oder hinten rutscht und der Klettverschluss verhindert eine Bewegung in die anderen Richtungen.
Um die Sichtbarkeit des Displays zu verbessern, wurden Kabelbinder verwendet.
Die Antenne des GPS-Moduls ist an der Seite des mechanischen Aufbaus montiert.
Die Halterung wird zur Inbetriebnahme in den mechanischen Aufbau gelegt und die Antenne wird mit dem GPS-Modul verbunden.
So ist Hardware unabhängig vom Aufbau und kann einfach gewartet werden.
Außerdem können fast alle Module nach dem Projekt wieder verwendet werden.\\
Problematisch am Aufbau ist, dass er durch die vielen Kabel sehr unübersichtlich ist.
Ein festes Verlöten der Module auf der Platine wäre eine Verbesserung.

\input{softwarearchitektur.tex}

\input{Projektbericht_Frontend.tex}

\subsection{Elektronik}
\chapterauthor{Lukas Eigenstetter}
Ein wichtiger Teil des Projektes war der Aufbau der Elektronik.\\
Diese umfasst zum einen die Stormversorgung der Controller und Sensoren.
Zusätzlich wurde ein Ladegerät, das den Strom vom Solar-Panel in den Akku steuert, entworfen.
Um eine genaue Regelung zu erlauben, mussten ein Messschaltkreis gebaut werden.
Da Strommessungen über Spannungsabfall an Shunts sehr ungenau sind, wurde zusätzlich ein Coulomb-Counter entworfen und verbaut.\\
In diesem Kapitel werden die umgesetzten Schaltkreise und deren Steuerung in Software erklärt.
Zusätzlich werden Probleme und Alternativen erklärt.\\
Die komplizierteren Schaltkreise wurden zunächst mit dem Falstad Circuit Simulator Applet getestet. \autocite{falstad}
Dies ist Umgebung, die ein einfaches Entwerfen und Testen erlaubt.
Die Abbildungen der Teilschaltpläne wurden auch mit dieser Software erstellt.

\subsubsection{Stromversorgung}
\chapterauthor{Lukas Eigenstetter}
Die Stromversorgung für Controller und Sensoren wird mittels eines Linearreglers realisiert.
Dieser reguliert die nicht konstante Batteriespannung, die im Bereich von 7 - 8.4 V liegen kann, auf einen konstanten Wert von 5 V.
Verbaut wurde ein Regler vom Typ 7805CV.\\
Die standardmäßige Schaltung sieht einen 330 nF Kondensator am Eingang V\_IN und einen 100 nF Kondensator am Ausgang vor. \autocite{linearregler}
Verbaut wurden Kunststofffolienkondenstoren.\\
Zusätzlich sind am Ein- und Ausgang 100 \textmu F Aluminium-Elektrolytkondensatoren verwendet.
Der Eingangskondensator dient dazu, Spannungserhöhungen- und Abfälle durch Veränderungen in der Batteriespannung abzufedern.
Durch den Ausgangskondensator werden Verbrauchsspitzen abgefedert.\\
Der Linearregler kann dauerhaft einen Ausgangsstrom von etwa 500 mA erzeugen.
Dieser Strom reicht zur Versorgung der Module und des Displays aus.\\
Tabelle \autoref{PowerConsumption} zeigt den gemessenen Verbrauch der Module.

\begin{table}[H]
    \begin{center}
        \begin{tabular}{|l|l|l|}
            \hline
            Modul                 & Stromverbrauch in mA       & Spannung in Volt \\
            \Xhline{3\arrayrulewidth}
            GPS                   & 100                        & 5.0              \\
            \hline
            Beschleunigungssensor & 0                          & 3.3              \\
            \hline
            Kompass               & 0                          & 3.3              \\
            \hline
            Display               & 0 - 5 (je nach Helligkeit) & 5.0              \\
            \hline
            SD-Card               & 40                         & 5.0              \\
            \hline
            Temperatursensor      & 0                          & 3.3              \\
            \hline
            ESP32                 & 40 - 60 (je nach Last)     & 5                \\
            \hline
        \end{tabular}
        \caption{Gemessener Stromverbrauch der Module\\
            Der gesamte Stromverbrauch liegt im Betrieb deutlich über 200 mA.}
        \label{PowerConsumption}
    \end{center}
\end{table}

Laut Datenblatt soll das GPS-Modul lediglich mit maximal 3.6 V versorgt werden.
Aufgrund des hohen Verbrauchs führt dies dazu, dass der Linearregler eines ESP32, der etwa 80 mA abgeben kann, nicht ausreicht.
Da das Modul einen USB Anschluss und einen eigenen Regler besitzt, ist es möglich auch 5 V zu verwenden.
Daher wurde dieses Modul ebenfalls an die 5 V Quelle angeschlossen.\\
Der hohe Stromverbrauch des Systems führt dazu, dass im realistischen Betrieb nur unter guten Wetterbedingungen mehr Strom produziert als verbraucht wird.
Um langfristig eine positive Energiebilanz zu erreichen, müssten Display, GPS und die weiteren Module ausschaltet und nur durch eine Nutzereingabe aktiviert werden.
Diese Verbesserung konnte nicht mehr realisiert werden.\\
Ein weiteres Problem bei der Stromversorgung ist die Verwendung zu dünner Kabel.
Alle Verbindungen wurden mittels der im Labor verfügbaren Jumperkabel realisiert.
Dies hat den Vorteil, dass die Sensoren für zukünftige Projekte weiter verwendet werden können.
Ein festes Verlöten der Module wäre eine sinnvolle Alternative gewesen, da so der Widerstand durch die Kabel und Stecker vermieden wird.
Zudem hätte dies für eine höhere Übersichtlichkeit des Aufbaus gesorgt.

\subsubsection{High Power Circuit}\label{HPC}
\chapterauthor{Lukas Eigenstetter}
Da die Servos und die USB-Schnittstelle einen deutlich höheren Stromverbrauch als die Module haben, wurde zusätzlich zum Linearregler eine Buck-Converter Schaltung verbaut.
Diese basiert auf einem LM2576ADJ Spannungsregler im TO-220 Format. \autocite{buckConverter}
Im Gegensatz zum Linearregler, der kurzzeitig 1.5 A und langfristig nur 500 mA liefert, kann der Buck Converter dauerhaft 3 A Ausgangsstrom erzeugen.
Mit einer Verlustleistung von etwa 20 Prozent ist dieser deutlich energieeffizienter als der Linearregler, der etwa 40 Prozent Verlustleistung hat.
Die Variante \emph{ADJ} hat den Vorteil, dass die Ausgangsspannung durch einen Feedbackwiderstand eingestellt werden kann.
Der Feedbackanschluss ist durch einen Spannungsteiler von 2.85 k\textOmega \ und 910\textOmega so eingestellt, dass im Freilauf minimal mehr als 5 V Ausgangspannung erzeugt werden.
Der Spannungsregler kann durch einen PIN ausgeschaltet werden, was etwa bei der Nachtabschaltung und für die Kalibrierung des State of Charge verwendet wird.\\
Nachteilhaft ist jedoch, dass dieses Bauteil ein PWM von 52 kHz erzeugt und so den den DCF-77 Empfänger stört.
Dies ist ein weiterer Grund, weshalb das DCF-77 Modul nicht im finalen Aufbau verwendet wird.\\
An den Ausgang muss daher eine Filterschaltung gebaut werden.
Diese besteht aus mehreren Aluminium-Elektrolytkondensatoren, die in Summe 1 mF haben und einer 6 A 0.1 mH Spule.\\
Da keine Zenerdiode verfügbar war, wurde eine NP-Diode vom Typ BY-255 als Freilaufdiode verwendet.
So wird die Beispielschaltung aus dem Datenblatt mit den vorhandenen Mitteln so gut wie möglich realisiert. \autoref{buckConverter} zeigt die Schaltung aus dem Datenblatt.

\begin{figure}[htpb] % {H}
    \centering
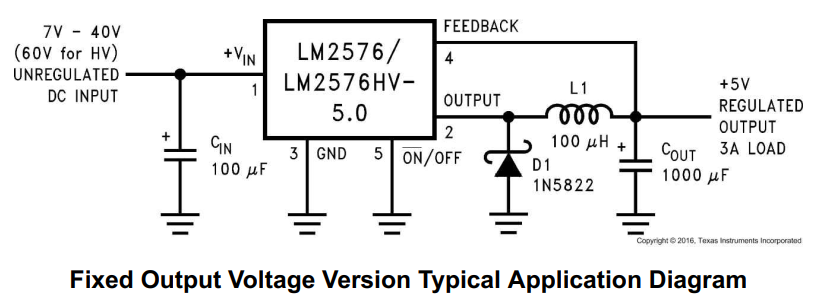
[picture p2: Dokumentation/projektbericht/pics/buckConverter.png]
    
    \caption{Schaltplan des Buck Converters \autocite{buckConverter}}
    \label{buckConverter}
\end{figure}

Unter Last kommt es bei´der Benutzung des High-Power-Circuits zu hohe Spannungsabfällen von etwa 1 V.
Diese führen dazu, dass der Controller neu startet.
Die Verwendung der falschen Diode ist der wahrscheinlichste Grund für die starken Spannungsschwankungen unter Last.
Dieses Problem konnte bis zur Abgabe nicht behoben werden. \\
Ein weiteres Problem ist, dass die verwendeten Akkus lediglich eine dauerhafte Entladerate von 1 C haben, was bei 2000 mAh einen Strom von 2 A zu Folge hat.
Daher kann die Leistungsfähigkeit des LM2576 nicht ausgenutzt werden.\\
Die Benutzung der USB-Schnittstelle oder der Servos bei Verwendung des High Power Circuits führt daher zum Absturz.
Zur Abnahme wurden die Servos direkt an einen 2 s LiPo Akku angeschlossen.

\subsubsection{Akkuladegerät}\label{akkuCircuit}
\chapterauthor{Lukas Eigenstetter}
Das Akkuladegerät dient zum Laden von Akkus mithilfe der vom Solarpanel produzierten Energie.
Es orientiert sich an einem Blogpost zu einem Arduino-Ladegerät. \autocite{microfarat}
In diesem Kapitel werden die Schaltung und die Formeln zur Berechnung der Werte erklärt.\\
Der Strom wird am Haupt-ESP mithilfe eines PWM-Signals gesteuert.
Das Signal schaltet einen BC547 Bipolartransistor. \autocite{bipo}
Ist der Transistor auf Durchlass geschaltet, so wird der MOSFET, der den Ladestrom steuert, ausgeschaltet.
Als Leistungstransistor wurde ein IRF5305 im TO-220 Format verwendet. \autocite{irf}
Da die Batterie Schwingungen ausreichend dämpft, wurde keine zusätzliche Filterschaltung verbaut.
Vor den Akku wurde eine BY-255 Diode in Laufrichtung eingebaut, um Strom von der Batterie zu den Panelen zu verhindern.
Abbildung \autoref{charger} zeigt verbaute Schaltung. \\

\begin{figure}[htpb] % {H}
    \centering
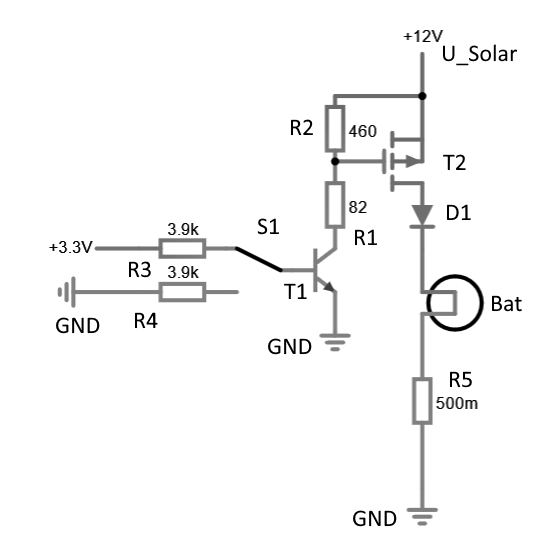
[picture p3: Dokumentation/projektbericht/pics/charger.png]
    
    \caption{Schaltplan des Lade-PWM}
    \label{charger}
\end{figure}

Zusätzlich wurde Cell-Balancing realisiert.\\
Bei Lithium Polymer Akkus tritt das Problem auf, dass einzelne Zellen unterschiedlich schnell verschleißen.
Dann verliert eine Zelle schneller an Kapazität als die andere, wodurch die Verschlissene schneller ge- und entladen wird.
Die Zelle mit der geringeren Kapazität kann dann überladen oder zu tief entladen werden, wenn nur die Gesamtspannung gemessen wird.\\
In SunStorage wurde ein einfaches, passives Cell-Balancing umgesetzt. 
Es wird jeweils die Spannung der Zellen gemessen und miteinander verglichen.
Falls eine Zelle eine deutlich höhere Spannung als die Andere aufweist, wird sie über einen 82\textOmega \ Widerstand entladen, bis sich ein Gleichgewicht hergestellt hat. 
Dieses Verfahren wird auch als \emph{Current Bypass} bezeichnet. 
Die Spannungsdifferenz, ab der Balancing aktiviert wird, kann im Frontend eingestellt werden. \autocite[S. 111 - 127]{chargerBuch}\\
\begin{figure}[htpb] % {H}
    \centering
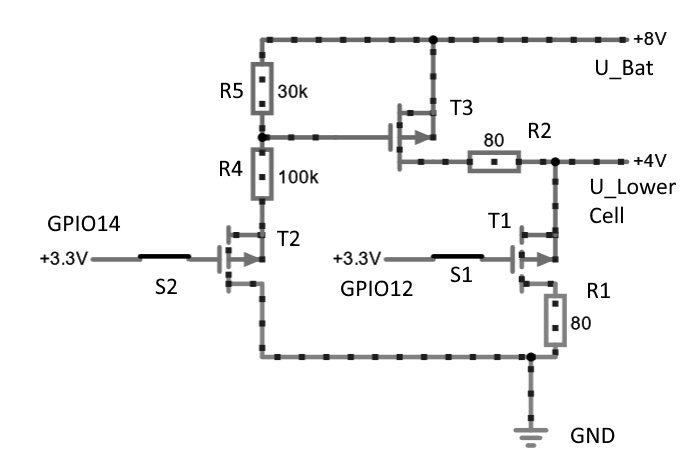
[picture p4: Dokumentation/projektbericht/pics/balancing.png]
    
    \caption{Schaltplan Cell Balancing}\label{balancing}
\end{figure}

\autoref{balancing} zeigt die Schaltung, die das Cell-Balancing umsetzt.
Für die niedrigere Zelle wird der Transistor T1 Transistor direkt über GPIO12 geschaltet.
Da die obere Zelle auf +4 bis +8 Volt liegt und der PIN nur 3.3 Volt liefert, muss für die obere Zelle eine Schaltung mit zwei Transistoren verwendet werden.
T2 dient zur Herstellung der für den Schaltvorgang von T3 notwendigen Spannung.
Über T3 wird die obere Zelle entladen.
Da P-Kanal-Transistoren verwendet werden, ist die Logik der Schaltung negativ.
Sind die PINs beispielsweise HIGH, so fließt kein Strom.\\
Verbaut wurden IRLML2244 Transistoren im SMT Format. \autocite{irlml}
Um sie in ein Put-Through-Board zu integrieren, wurden sie zunächst an dickere PINs gelötet, die dann an das Board gelötet wurden.\\

Zur Messung der Spannungen und Ströme werden die ADC des Haupt-ESP verwendet.
Der Ladestrom kann über die an R8 abfallende Spannung gemessen werden.
Ist die Spannung positiv, so fließt Strom aus der Batterie in das System. Ist sie negativ, so wird mehr produziert als konsumiert und die Batterie wird geladen.
\autoref{messaufbau} zeigt den Teil des Systems, der für die Messungen relevant ist.
$I_{Solar}$ ist dabei der Strom des Panels und S1 symbolisiert das PWM Signal des Ladegeräts.
$R_{Sys}$ ist der Widerstand des Systems.
So wird der Stromverbrauch modelliert.
Aus Gründen der Übersichtlichkeit wurde auf die zwischen ADC- und GND geschalteten 100 nF Kondensatoren, die das Rauschen verringern, nicht eingezeichnet.
Der vollständige Schaltplan ist in \autoref{schaltplanHaupt} dargestellt.

\begin{figure}[htpb] % {H}
    \centering
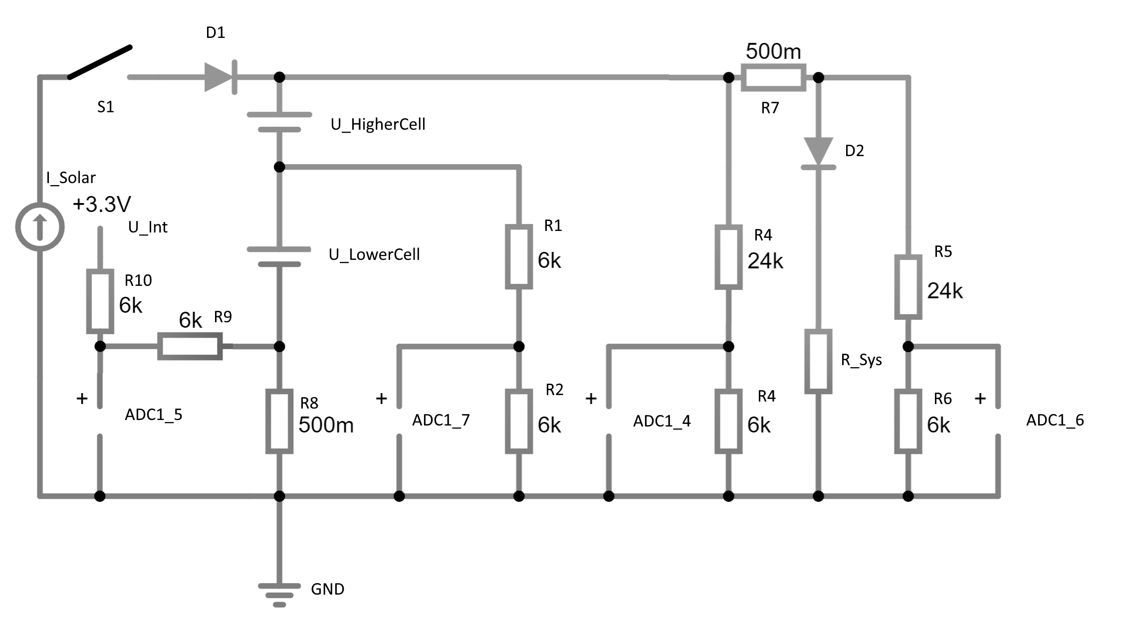
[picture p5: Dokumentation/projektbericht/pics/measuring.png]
    
    \caption{Schaltplan des Messungsaufbau}
    \label{messaufbau}
\end{figure}

Da negative Spannungen nicht im Ansteuerbereich des ADC liegen, muss eine Pullupschaltung verwendet werden.
Mithilfe von R9 und R10 wird die Spannung am ADC auf 1.65 V gezogen.
Die tatsächlich am Widerstand anliegende Spannung muss daher um 1.65 V verringert werden:
$$ U_{ChargerShunt} = U_{0} - U_{ADC1\_5} $$
Der Ladestrom  ergibt sich durch die folgende Formel:
$$ I_{Charger} = I_{System} + U_{ChargerShunt} \cdot c_{SysSh}  $$

Die Konstanten können \autoref{adcCali} entnommen werden.
Die Spannung der niedrigeren Batteriezelle ergibt sich durch die Messung von ADC1\_7.
Um die Werte im Ansteuerbereich zu halten, wird ein Spannungsteiler aus R1 und R2 gebaut.
Zusätzlich muss die an R8 abfallende Spannung berücksichtigt werden.
Daraus ergibt sich die folgende Formel:
$$ U_{LowerCell} = (U_{ADC1\_7} + U_{ChargerShunt} \cdot \frac{c_{CharSh}}{c_{LC}}) \cdot c_{LC} $$
Für die Berechnung der Gesamtspannung wurde die selbe Schaltung verwendet.
Lediglich R4 muss erhöht werden, um den Spannungsbereich von ADC1\_4 zu erreichen.
Auch hier muss die Spannung an R8 berücksichtigt werden:
$$ U_{Battery} = (U_{ADC1\_4} + U_{ChargerShunt} \cdot \frac{c_{CharSh}}{c_{HC}}) \cdot c_{HC} $$
Mithilfe der Spannungen an ADC1\_6 und ADC1\_4 kann der Strom durch D2 und R\_Sys berechnet werden.
Die Diode wird in Laufrichtung betrieben und verhindert, dass Strom vom System in die Batterie fließt.
Dies könnte beispielsweise passieren, wenn ein PC zum Flashen oder Monitoring angeschlossen ist.
R\_Sys beschreibt vereinfacht den Widerstand des Systems.
Die Differenz aus der Spannung an ADC1\_4 und ADC1\_6 ist die an R7 abfallende Spannung und damit der Systemstrom.
Die konkrete Formel lautet:
$$ I_{System} = (U_{ADC1\_4} \cdot c_{HC} - U_{ADC1\_6} \cdot c_{SysDiv}) \cdot c_{SysSh} $$
Da die Widerstände nicht genau die Werte der Zeichnung besitzen, musste das Gesamtsystem kalibriert werden.
Dies wurde durch Messungen der Ströme und Spannungen mithilfe von Multimetern umgesetzt.
Da keine 6 k\textOmega \ Widerstände vorhanden waren, wurden 6.4 k\textOmega \ Widerstände verbaut. Diese weisen relativ hohe Abweichungen auf, weshalb die Kalibrierungswerte deutlich von den berechneten Werten abweichen.
Die Kalibrierungswerte des Endsystems lauten:

\begin{table}[H]
    \begin{center}
        \begin{tabular}{|l|l|l|r|}
            \hline
            Beschreibung                   & Symbol         & Variablenname                  & Wert \\
            \Xhline{3\arrayrulewidth}
            Pullup des Ladestroms          & $ U_{0} $      & VOLTAGE\_SOLAR\_0              & 1650 \\
            \hline
            Shunt für Ladestrom            & $ c_{SysSh} $  & SOLAR\_SHUNT\_TO\_AMPS         & 2.0  \\
            \hline
            Shunt für Verbrauch            & $ c_{CharSh} $ & SYSTEM\_SHUNT\_TO\_AMPS        & 2.0  \\
            \hline
            Spannung der niedrigeren Zelle & $ c_{LC} $     & VOLTAGE\_DIVIDER\_LOWER        & 2.26 \\
            \hline
            Spannung der Batterie          & $ c_{HC} $     & VOLTAGE\_DIVIDER\_BATTERY      & 4.05 \\
            \hline
            Spannung Verbrauchsmessung     & $ c_{SysDiv} $ & VOLTAGE\_DIVIDER\_SYS\_CURRENT & 3.65 \\
            \hline
        \end{tabular}
        \caption{Kalibrierung der ADC Berechnungsparameter}
        \label{adcCali}
    \end{center}
\end{table}

Zum Auslesen der ADC wird die ADC-Oneshot-API der Espressif IDF verwendet.
Da die ADC Messwerte Ausschläge von bis zu 30 mV aufweisen, wird ein gleitender Mittelwert aus den letzten Messungen gebildet.
Dafür werden zu jedem Zeitpunkt die letzten zehn Werte betrachtet, wobei der Höchste und der Niedrigste verworfen werden.
Aus den restlichen acht Werten wird der Mittelwert gebildet.
Durch die Mittelwertbildung können die Schwankungen der Messungen ausgeglichen werden.
Aufgrund der gleichzeitigen Nutzung des WiFi konnten nur PINs des ADC1 verwendet werden.\\
Die zehn letzten Werte liegen im Programm in einem Ringbuffer vor.
Um das Minimum und das Maximum zu bestimmen, wird dieser kopiert und die Kopie wird sortiert.
Alle Berechnungen werden mit Fixkommazahlen im Milli-Bereich durchgeführt.\\
Problematisch an dieser Vorgehensweise ist zum einen, dass kurze Spannungspitzen möglicherweise nicht registriert werden.
Außerdem wirken sich Veränderungen der Messwerte erst mit einer gewissen Verzögerung erkennbar auf den Ergebniswert aus.
Diesen Effekten wird durch eine Erhöhung der Abtastrate von 1 Hz auf 10 Hz entgegengewirkt.

Die in diesem Kapitel erklärten Berechnungen sind in der Simulation korrekt.
In \autoref{fig:graphen} ist erkennbar, dass die tatsächlich gemessenen Werte falsch sind.
Zum einen sind die Ströme zu hoch.
Dies führt dazu, dass unter Last auch die Spannungsmessungen verfälscht werden.
Der genaue Grund konnte bis zum Ende des Projekts nicht gefunden werden.
Es könnte entweder an einem nicht berücksichtigten Faktor und damit einem Fehler in der Simulation und Modellierung liegen.
Eine weitere Möglichkeit ist ein Fehler in der Umsetzung des Schaltkreises.

\subsubsection{USB-Schnittstelle}\label{usbSchnittstelle}
\chapterauthor{Lukas Eigenstetter}
Die USB Schnittstelle wird durch den High-Power-Circuit (\autoref{HPC}) versorgt.
Die grundlegenden Lademodi in den meisten Handys werden durch das Anlegen einer bestimmten Spannung an den mittleren PINs des USB Ports festgelegt.
Für höhere Ladeströme gibt es spezielle Protokolle wie beispielsweise \emph{Quick Charge}. \autocite{quickCharge}
\autoref{UsbModi} zeigt die umgesetzten Modi und die verwendeten Schwellspannugen.

\begin{table}[H]
    \begin{center}
        \begin{tabular}{|l|r|r|}
            \hline
            Modus          & PIN 1 & PIN 2 \\
            \Xhline{3\arrayrulewidth}
            500 mA (2.5 W) & 2.0 V & 2.0 V \\
            \hline
            1 A (5 W)      & 2 V   & 2.8 V \\
            \hline
            2,1 A (10 W)   & 2.8 V & 2.0 V \\
            \hline
        \end{tabular}
        \caption{Spannung an mittleren PINs in für den jeweiligen Lademodus. PIN 1 ist neben GND. \autocite{usbProtokoll}}
        \label{UsbModi}
    \end{center}
\end{table}

Je nach Modus werden die DAC Pins auf die passende Spannung gesetzt.
Der Buck-Converter kann laut Datenblatt dauerhaft einen Strom von 3 A liefern.
Damit ist der Stromkreis auch im 10 W Modus hinreichend versorgt.

\subsubsection{Coulomb-Counter}
\chapterauthor{Matthias Unterrainer}
\begin{figure}[htpb]
    \centering
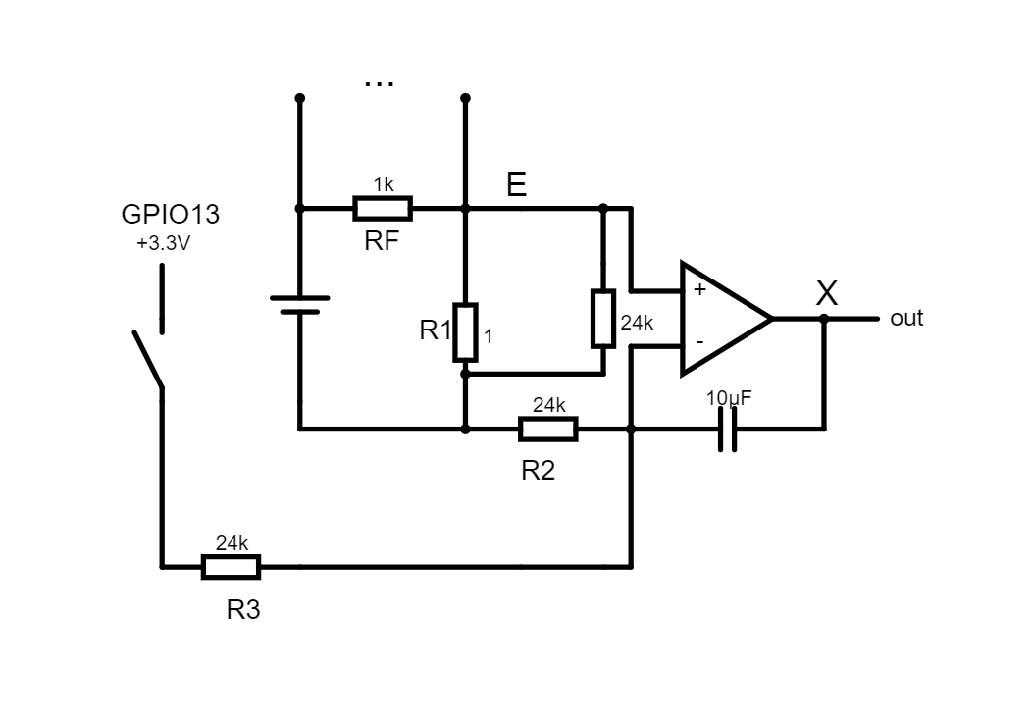
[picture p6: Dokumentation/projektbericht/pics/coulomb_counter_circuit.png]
    
    \caption{Schaltplan des Coulomb-Counters}
    \label{fig:coulomb_counter}
\end{figure}

Um effektiv den Stromfluss im Schaltkreis messen zu können, wurde ein Coulomb-Counter entworfen und eingebaut.
Ein Coulomb-Counter funktioniert im Pinzip so, dass ein bestimmter Strom durch einen Stromkreis fließt, dieser kann denn Akku laden oder entladen. Wenn jetzt die Ladung im Akku zu Beginn der Messung bekannt ist, dann kann allein durch das Wissen, wie viel Ladung ge-/entladen wurde, relativ genau bestimmt werden, wie viel Ladung im Akku noch übrig ist. Dazu wird der Strom mithilfe eines sehr kleinen Widerstandes $R_1$, unter dem ohmschen Gesetz $R = \frac{U}{I}$, welches die Beziehung zwischen Strom und Spannung beschreibt, in eine Spannung ''umgewandelt''. Da hier für $R_1$ ein Widerstand von 1 Ohm gewählt wurde, entspricht der Strom der durch den Widerstand fließt der über den Widerstand anliegenden Spannung. Da der Coulomb-Counter jedoch für Ströme bis zu 2 A ausgelegt sein sollte, was zu einer Spannung von 2 V führen würde, musste diese, aufgrund der Funktionsweise des Op-Amps, noch durch einen Spannnungsteiler reduziert werden. Hierbei wurde die Eingangsspannung durch den Spannungsteiler der sich aus $R_F$ und $R_1$ zusammen setzt, wobei $R_F$ 1 k$\Omega$ ist, auf ca. $\frac{1}{1000}$ der Eingangsspannung reduziert. Genauer auf $V_{\text{in}} \cdot \frac{1 \Omega}{1000 \Omega + 1 \Omega} = 0.\overline{000999} \cdot V_{\text{in}}$. Dadurch wird die maximale Eingangsspannung bei einer maximal Last von 2 A auf 2 mV begrenzt.\\\\
Dies ist jedoch erst der erste Schritt, da bis jetzt nur eine Spannung äquivalent zu ca. $\frac{1}{1000}$ der Eingangsspannung an der Stelle $E$ gemessen werden kann. Dies beschreibt lediglich den aktuellen Strom, der in diesem Moment durch den Stromkreis fließt, enthält aber noch keine Informationen über die zeitliche Komponente, also darüber, wie viel Strom in einer bestimmten Zeit durch den Stromkreis geflossen ist. Um diese aussagekräftigere Messung aus den einzelnen Momentanaufnahmen zu erhalten, müssen diese über die Zeit integriert werden. Dies wird mithilfe eines analogen Integrators bewerkstelligt. Dieser setzt sich aus einem Operationsverstärker (Op-Amp), dem LMC6462 Op-Amp, und einem 10 $\mu$F Kondensator zusammen.\\\\
\begin{figure}[htpb]
    \centering
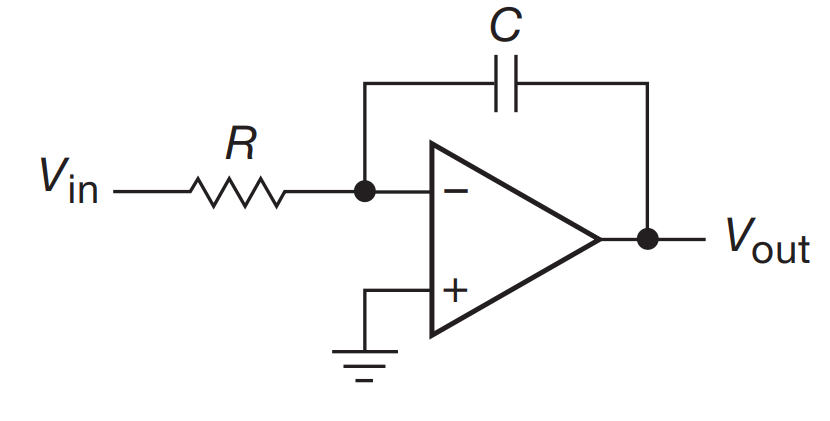
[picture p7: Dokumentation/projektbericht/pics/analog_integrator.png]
    
    \caption{Grundlegender Aufbau eines Op-Amp Integrators. \cite{aoe}}
    \label{fig:analog_integrator}    
\end{figure}
Abb. \ref{fig:analog_integrator} zeigt den Aufbau eines Op-Amp Integrators. Der Eingangsstrom $\frac{V_{\text{in}}}{R}$ fließt durch den Kondensator $C$, und da der invertierende Eingang ein virtueller Nullpunkt ist, wird die Ausgangsspannung durch
$$V_{\text{out}}(t) = - \frac{1}{RC} \int V_{\text{in}}(t) dt + \text{ const.}$$
gegeben. Daraus folgt
$$\Delta V_{\text{out}} = - \frac{V_{\text{in}}}{RC} \Delta t = - \frac{I_{\text{in}}}{C} \Delta t$$ \cite{aoe}

\begin{figure}[htpb]
    \centering
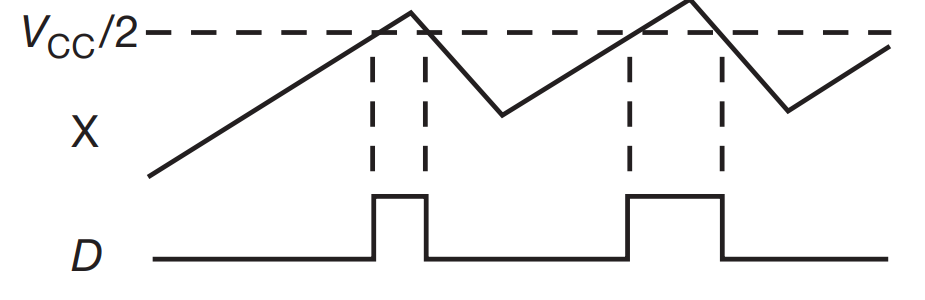
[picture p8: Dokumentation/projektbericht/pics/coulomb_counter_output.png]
    
    \caption{$X$ ist der Output des Integrators, $V_{CC}$ ist hier 3.3 V und $D$ ist der resultierende Duty-Cycle. \cite{aoe}}
    \label{fig:coulomb_counter_output}    
\end{figure}

In Abb. \ref{fig:coulomb_counter_output} ist der Output des Integrators ($X$) zu sehen. Dieser wird mit einer festen Spannung (hier $\frac{V_{CC}}{2}$, was aber für die entgültige Rechnung unwichtig ist) verglichen und aus der Zeit die $X$ größer als die Vergleichsspannung ist, wird ein Duty-Cycle $D$ abgeleitet. Da solange keine negative Spannung anliegt das Integral immer weiter steigt (zumindestens bis zur Obergrenze $V^+$), muss, wie in Abb. \ref{fig:coulomb_counter} zu sehen, der Integrator regelmäßig ''entladen'' werden. Dies geschiet via einer ''Entladespannung'', die hier über den GPIO-Pin 13 angelegt wird. Da wie bereits erwähnt der Output proportional zu $I_{in}$ bzw. $\frac{I_{in}}{C}$ steigt und proportional zu der ''Entladespannung'' $\frac{V_{CC}}{R_{3}} - \frac{I_{in}}{C}$ fällt, kann daraus die Länge des Duty-Cycles ermittelt werden. Da in diesem Entwurf, wenn der GPIO-Pin13 auf GND gezogen ist, $R_3$ und $R_2$ in parallel zu einander geschalten sind, entspricht der Widerstand beim ''Laden'' $R_{cha} = \frac{R_2 R_3}{R_2 + R_3} = \frac{24k\Omega \cdot 24k\Omega}{24k\Omega + 24k\Omega} = 12k\Omega$.  Daraus folgt, dass der Duty-Cycle $D$ über längere Zeit
$$D = \frac{I_{in} R_{3}}{C V_{CC}} \Rightarrow I_{in} = \frac{D \cdot C \cdot V_{CC}}{R_{3}}$$\cite{aoe}\\\\
Somit repräsentiert $I_{in}$ den Strom der durch das System seit Messbeginn geflossen ist.\\\\
Der LMC6462 Op-Amp wurde gewählt, da dieser einen kleinen Input Offset Voltage von nur 0.25 mV hat. Dies entspricht einem maximalen Offset Fehler von $e_{\text{off}} = \frac{V_{os}}{V_{in,max}} = \frac{250 \mu V}{2 V} = \frac{1}{8000}$ dies entspricht einem Messfehler von 25 mA ($2 A \cdot \frac{1}{8000} = 2.5 \times 10^-4$A) bzw. einer Auflösung von 8000:1. Und da dieser eine sehr niedrige Versorgung von nur 20$\mu$A / Amplifier benötigt.
Ein weiterer Grund für den LMC6462 war sein Rail-to-Rail Output mit einem maximalen Offset von diesem von unter 10 mV, da dadurch bei einem $V^+$ von 3.3 V der Output des Integrators nie 3.4 V überschreitet und somit den ADC Pin, der bis zu 3.9 V messen kann, nie überlasten wird. \cite{LMC6462_data_sheet} Und es wurde eine 10 $\mu$ F Kondensator gewählt, da der Coulomb-Counter Output mit 10Hz abgetastet wird, ergibt sich dass mit $R_3 = 12k\Omega, f = 10Hz, C = 10 \mu F$, dass der Integrator nie mit mehr als $C \cdot f \cdot R_3 = 10 \mu F \cdot 10Hz \cdot 12000 \Omega = 1.2$ also $\frac{V_{CC}}{1.2}$ pro Taktzyklus steigt oder fällt. \cite{aoe}

\paragraph{Probleme}
\chapterauthor{Matthias Unterrainer}
Das Hauptproblem mit dem Coulomb-Counter ist, dass zum einem der Input Rail-to-Rail ist, aber $V^- =$ GND und $V^+ = 3.3$ V ist. Dadurch kann generell keine negative Spannung, die beispielsweise beim Lade auftreten könnte, im Integral berücksichtigt werden, wodurch der Coulomb-Counter nur die Entladung richtig misst. Da aber das ganze Konzept von Coulomb-Counting darauf beruht, dass man genau darüber bescheid weiß, wie viel Ladung in den Akku rein- oder rausgeflossen ist, zerstört dies jeden Ansatz einer akuraten Messung.\\
Dies ist zwar generell ein Problem, aber in diesem Aufbau vernachlässigbar, da der Coulomb-Counter so eingebaut wurde, dass die zu messenden Spannung $V_{in} < 1.65 V$ beim Laden und $V_{in} > 1.65 V$ beim Entladen beträgt. Dieser Aufbau führt allerdings zu deutlich erheblicheren Problemen, da erstens, dass Integral dadurch von den Werten her verschoben wird, was zwar noch nachträglich lösbar ist, aber das Hauptproblem ist der zweite Punkt, dass dadurch vor allem beim Laden sehr kleine Spannungen anliegen. Dies ist ein Problem, da wie oben bereits erwähnt, der Coulomb-Counter auf 2 A ausgelegt wurde unde deshalb extra ein Spannungsteiler eingebaut wurde, um die ''Startspannung'' niedrig zu halten, damit eine akurate Messung möglich ist. Wenn jedoch nur eine Spannung von 0.1 V anliegt, was einer relative hohe Ladespannung entsprechen würde, dann liegen Aufgrund des Spannungsteilers nur etwa 0.1 mV am Op-Amp an. Es folgt daraus, dass um die Vergleichsspannung von 1.65 V zu erreichen, mit $\Delta V_{\text{out}} = - \frac{V_{\text{in}}}{R_{chr}C} \Delta t \Rightarrow \Delta t = \frac{\Delta V_{out} \cdot R_{chr} \cdot C}{V_{in}} = \frac{1.65 V \cdot 12 k\Omega \cdot 10 \mu F}{0.1 mV} = 1980 s = 33 min$. Es würde also über eine halbe Stunde dauern, um nur eine Spitze des Duty-Cycles zu erreichen, was ein großes Problem ist, da das ganze Konzept auf vielen kleinen Messungen basiert, welche zwar einzeln gesehen teilweise größere Abweichungen haben, aber in der Summe ein relativ gutes Gesammtbild schaffen.

\subsubsection{Realisierung}
\chapterauthor{Lukas Eigenstetter}
In diesem Kapitel wird die konkrete Realisierung der Schaltung beschrieben.
Dabei werden die Probleme und angewendeten Techniken beschrieben.\\

\paragraph{Haupt-ESP}
\chapterauthor{Lukas Eigenstetter}
Das Ladegerät und der Haupt-ESP sind auf einer 40 x 40 Put-Through Platine verlötet.
Diese besitzt durchgezogene Leiterbahnen auf der Unterseite.
Mithilfe eines Dremel-Schleifers wurden diese an bestimmten Stellen durchtrennt, um die gesamte Schaltung auf diesem Board unterzubringen.\\
\autoref{schaltplanHaupt} zeigt den Schaltplan.
Für Ein- und Ausgänge wurden jeweils PINs verlötet, die eine Verbindung mit Jumper-Kabeln erlauben.
Aus Platzmangel mussten am tatsächlichen ESP auch Leitungen zwischen Controller und Platine verbaut werden.
Diese sind in der Zeichnung direkt oberhalb des Controllers eingezeichnet.
Widerstände, die in Reihe geschaltet sind, und Draht der zur Verlängerung der Verbindungen einiger Bauelemente benötigt wurde, sind oberhalb der Platine verbunden.
Dies wurde durch Verdrillen und Verlöten gelöst.\\
Zusätzlich befindet sich auf dieser Platine die Stromversorgung und der Buck-Converter.
Um den Kapazität für das Filter des Abwärtswandlers zu realisieren, mussten sechs Kondensatoren parallel geschaltet werden.
Auch hier wurde das Verfahren des Verdrillens und Verlötens angewendet.
Um die Schaltung noch kompakter zu gestalten wurden die 1 \textOmega \ / 3 W Leistungswiderstände teilweise vertikal verbaut.

\begin{figure}[htpb] % {H}
    \begin{center}
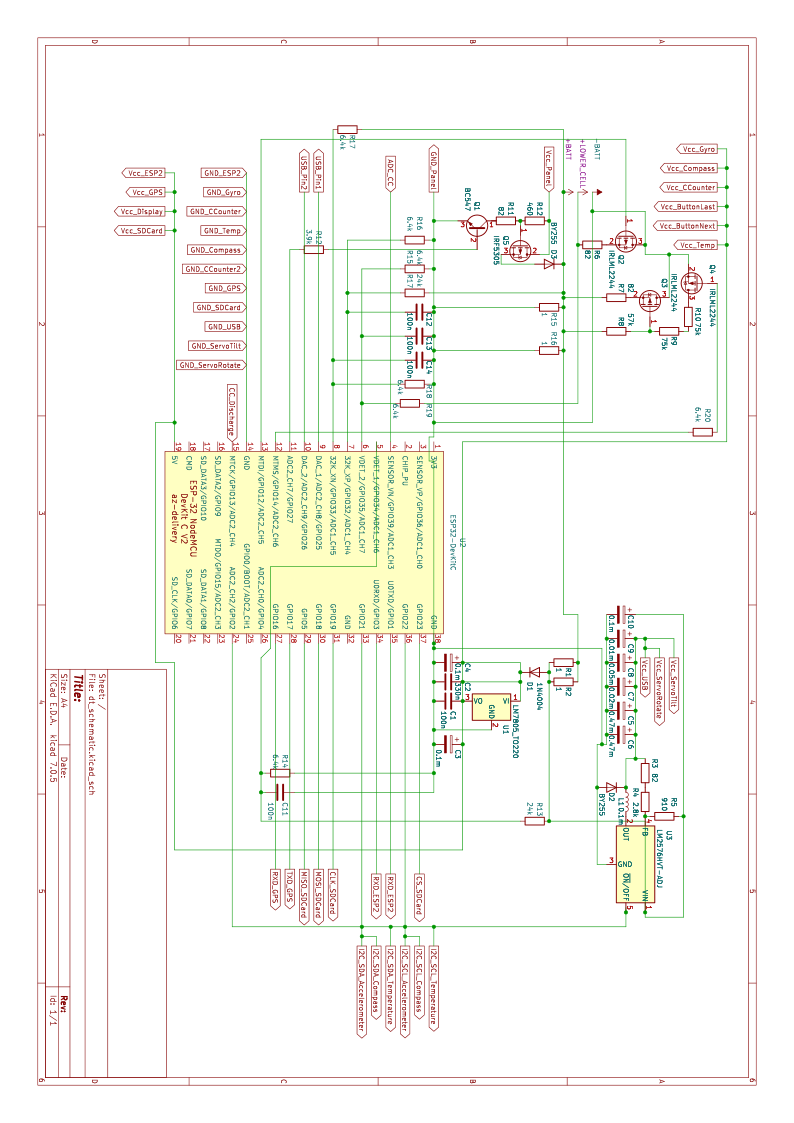
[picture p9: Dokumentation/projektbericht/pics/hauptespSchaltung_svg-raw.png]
        
        \caption{Schaltplan des Hauptcontrollers}
        \label{schaltplanHaupt}
    \end{center}
    Im Dokumentationsordner liegen ein SVG und die KiCad Datei zur besseren Lesbarkeit und Nachvollziehbarkeit bei.
\end{figure}
\clearpage

\paragraph{Neben-ESP}
\chapterauthor{Matthias Unterrainer}
Der Neben-Esp wird nur verwendet um die Servos und das LCD Display zu steueren. Dazu werden die notwendigen Daten via UART vom Haupt-Esp an den Neben-Esp geschickt.
\begin{figure}[htpb] % {H}
    \begin{center}
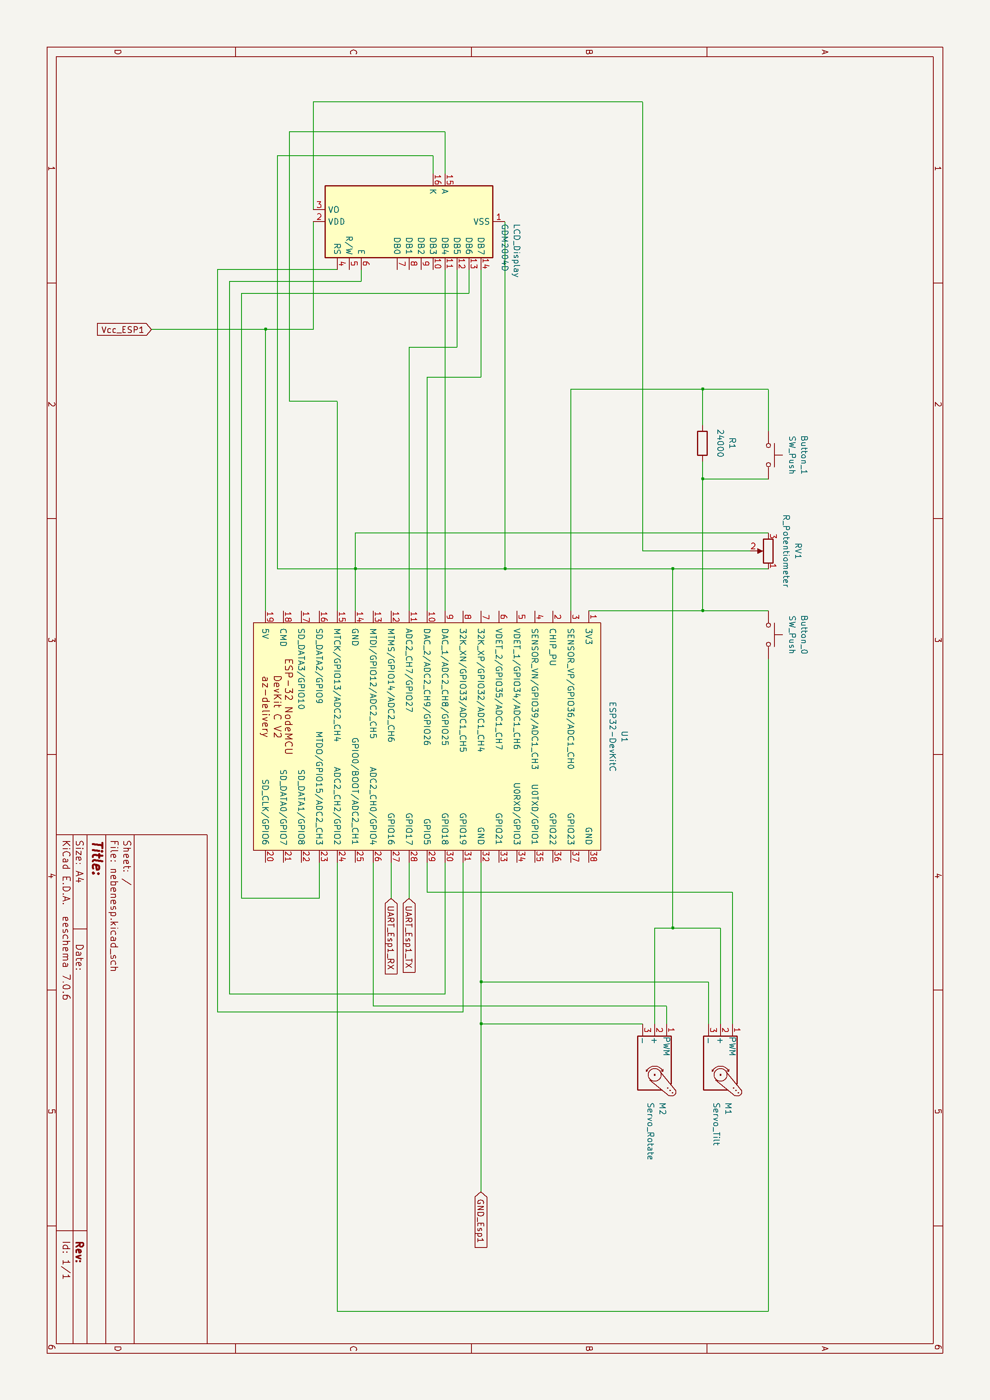
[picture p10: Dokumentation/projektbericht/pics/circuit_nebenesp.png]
        
        \caption{Schaltplan des Nebenesps}
        \label{curcit_nebenesp}
    \end{center}
    Im Dokumentationsordner liegen ein SVG und die KiCad Datei zur besseren Lesbarkeit und Nachvollziehbarkeit bei.
\end{figure}

\subsection{Datenverwaltung}
\chapterauthor{Philipp Thaler}
Das Projekt SunStorage hat verschiedene Systemzustände und muss auch historische Daten speichern können. Zudem kann auch die WLAN Konfiguration bearbeitet werden.
Um diese Funktionen bereitzustellen ist es nötig, dass das System über eine Datenverwaltung verfügt.

Die folgenden Kapitel geben einen detailierten Einblick, wie das System intern Daten speichert und verwendet.

\input{spiffs.tex}

\input{CSV-Historie.tex}

\subsubsection{Systemzustand}\label{Systemzustand}
\chapterauthor{Lukas Eigenstetter}
Der Systemzustand beschreibt alle Werte, die zwischen Neustarts des Systems erhalten bleiben sollen, für die keine Historie benötigt wird.
So können Konfigurationswerte aus dem Frontend erhalten bleiben.
Weitere Zustandsinformationen umfassen zuletzt gelesene Sensorwerte oder Stellwerte der Servos.\\
Der Zustand wird durch ein JSON-Objekt realisiert, das die Daten als Singleton hält und einen synchronisierten Austausch ermöglicht.
Beim Systemstart wird versucht, die Datei \textbf{state.txt} auf der SD-Card zu lesen und als JSON zu parsen.
Falls die Datei einige Werte nicht enthält oder fehlt, werden Defaultwerte verwendet.\\
Im Betrieb wird der Zustand alle 5 Sekunden geschrieben.
\autoref{tableStateCharger} zeigt alle Werte mit Bezug zum Ladegerät, die im finalen Zustandsobjekt enthalten sind.\\
\begin{table}[H]
    \begin{center}
        \begin{tabular}{|l|l|}
            \hline
            Name                  & Beschreibung                                           \\
            \Xhline{3\arrayrulewidth}
            usbMode               & Modus der USB-Schnittstelle (siehe \autoref{UsbModi})  \\
            \hline
            chargerMode           & Zustand des Ladegerätes (siehe \autoref{stmAkkulader}) \\
            \hline
            currentTarget         & Angestrebter Ladestrom                                 \\
            \hline
            thresholdVoltage      & Hysterese gegenüber Maximalspannung                    \\
            \hline
            maximumVoltage        & höchste Spannung, bis zu der geladen wird              \\
            \hline
            trickleThreshold      & Spannung, ab der der Ladevorgang verlangsamt wird      \\
            \hline
            batterySize           & Kapazität des Akkus in mAh                             \\
            \hline
            overheatedTemperature & Temperatur, bei der der Ladevorgang abgebrochen wird  \\
            \hline
            overheatedHysteresis  & Hysterese relativ zur overheatedTemperature              \\
            \hline
            highPowerEnabled      & High Power Circuit eingeschaltet                       \\
            \hline
        \end{tabular}
        \caption{Zustandsattribute für Ladegerät}
        \label{tableStateCharger}
    \end{center}
\end{table}
Da der State außerdem als Kommunikationsschnittstelle zwischen lesenden und schreibenden Tasks dient, wird für jedes Objekt ein Getter und ein Setter definiert.
So wird zusätzlich die JSON Struktur von der Verwendung im Programm abstrahiert werden.
Um ein Reader-Writer-Problem zu verhindern, wird der Zugriff über eine Semaphore gesichert.\\
Da erst spät erkannt wurde, dass ein zweiter Controller benötigt wird, wurde kein separates Protokoll für den Datenaustausch mehr definiert.
Durch ein regelmäßiges Übertragen des Zustands wird der zweite Controller gesteuert.
Eine saubere Lösung der Kommunikation wird in \autoref{KommunikationVerbesserung} beschrieben.

\input{kommunikation.tex}

\subsection{Module}
\chapterauthor{Johannes Treske}
Dieses Kapitel beschäftigt sich mit den im System verbauten Sensoren, Servos und dem verbauten Display.
Des Weiteren wird Bezug auf die dazu geschriebenen Treiber genommen.

\input{sensoren.tex}

\subsubsection{DCF-77}
\chapterauthor{Matthias Unterrainer}
DCF-77 ist ein weit verbreiteter Langwellenzeitcode in Mitteleuropa. Er wird von der von der Physikalisch-Technischen Bundesanstalt (PTB) aus Frankfurt, Deutschland, betrieben. Der DCF-77 sendet ein Zeit- und Datensignal auf einer Frequenz von 77,5 Kilohertz, wobei jede Sekunde ein Bit übertragen wird, also insgesamt 60 Bit pro Minute, was einem Datensatz entspricht. \cite{dcf77_logs}
\begin{figure}[htpb] % {H}
    \centering
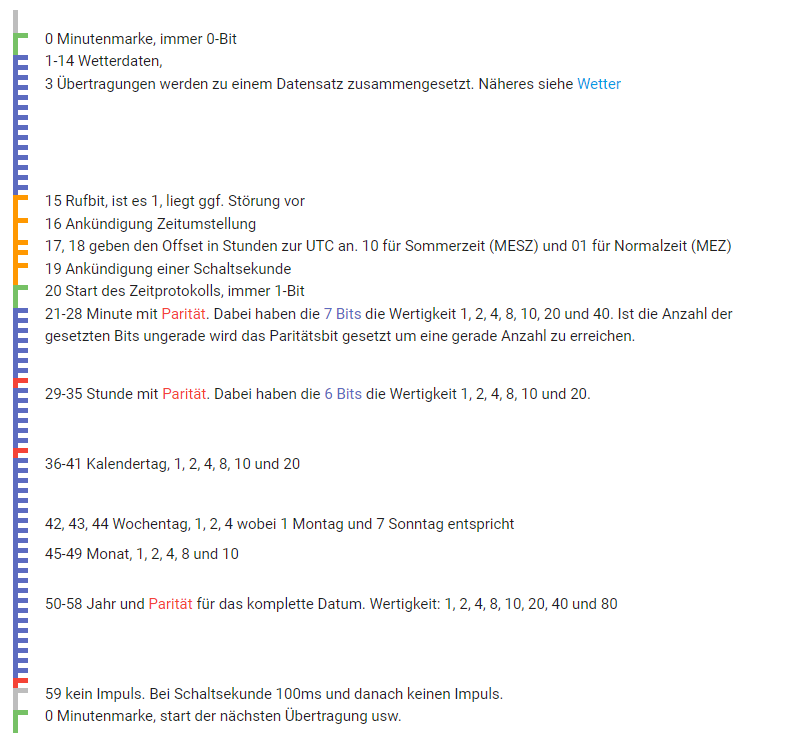
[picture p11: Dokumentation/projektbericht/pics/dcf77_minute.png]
    
    \caption{Aufbau einer Minute. \cite{dcf77_logs}}
    \label{fig:dcf77_minute}
\end{figure}
Wie in \autoref{fig:dcf77_minute} zu erkennen besteht ein Datensatz grob aus Wetterdaten und der aktuellen Zeit, die sich aus Datum und Uhrzeit zusammen setzt, und noch einigen weiteren Informationen über beispielsweise Sommer-/Winterzeit.
Täglich werden dabei 480 Wetterdatensätze für 90 Regionen gesendet, wobei 60 Regionen eine Vier-Tage-Vorhersage und 30 Regionen eine Zwei-Tagen-Vorhersage erhalten. Die Übertragung der Wetterdaten beginnt täglich um 22 Uhr UTC mit Region 0. Für die ersten 60 Regionen werden für die ersten drei Tage sowohl die Höchst- als auch die Tiefstwert übertragen, während am 4. Tag nur noch der Höchstwert gesendet wird. Die freien Kapazitäten, die durch das Weglassen des Tiefstwerts am 4. Tag entstehen, werden genutzt, um für die restlichen 30 Regionen die Höchstwerte für die nächsten zwei Tage zu übermitteln. Ein ''Wetterbericht'' setzt sich dabei aus jeweils drei Einzelübertragungen zusammen. \cite{dcf77_wetter}
\begin{figure}[htpb] % {H}
    \centering
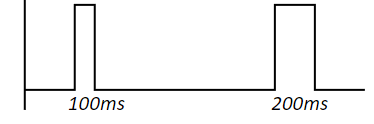
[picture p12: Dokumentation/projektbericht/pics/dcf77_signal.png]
    
    \caption{Vom DCF77-Reciever auslesbares Signal. \cite{dcf77_logs}}
    \label{fig:dcf77_signal}
\end{figure}
In Abb. \ref{fig:dcf77_signal} ist das vom DCF-77 Reciever Modul ausgegebene Signal zu sehen. Wobei deutlich zu erkennen ist, dass zum Beginn einer Sekunde der Ausgang entweder für 100ms (bei einem 0-Bit) oder 200ms (bei einem 1-Bit) auf \textit{HIGH} gezogen wird und dann für die restliche Sekunde auf \textit{LOW} bleibt. Um dieses Signal ordnungsgemäß auslesen zu können, müsste es gemäß dem Abtasttheorem mit mindestens 20 Hz abgetastet werden, da das kürzeste Signal 100 ms lang ist, also mit einer Frequenz von 10 Hz läuft. Dies würde jedoch bedeuten, dass der DCF-77-Lesetask mindestens alle 50 ms oder sogar noch häufiger gestartet werden müsste, um sicherzustellen, dass das Signal korrekt erkannt wird. Um allerdings genutzt werden zu können, müsste dieser Task auf dem Haupt-ESP laufen, da ansonsten aufgrund der Tatsache, dass die Kommunikation vom Haupt-ESP zum Neben-ESP unidirektional ist, die vom DCF-77 gelieferten Daten größteils ungenutzt bleiben würden. Auf dem Haupt-ESP werden jedoch bereits einige andere wichtige Tasks ausgeführt und das ständige starten des DCF-77 Tasks hat zu erheblichen Problemen beim Scheduling geführt, da der DCF-77 Task für mindestens eine ganze Minute ein sauberes Signal erkennen muss, um eine genaue Messung zu ermöglichen. Dies hat verhindert, dass der DCF-77 Task kontinuierlich laufen kann. 
Es wurde die Idee diskutiert, den Task nur zu bestimmten Uhrzeiten am Tag laufen zu lassen, um nur den ''Wetterbericht'' für die entsprechende Region vom DCF-77 zu erhalten, da die Uhrzeit sowieso viel genauer vom GPS empfangen wird, in Sekunden statt nur in Minuten wie beim DCF-77. Da allerings wie bereits erwähnt, ein einzelner ''Wetterbericht'' aus drei vollständigen Übertragungen besteht, die alle empfangen werden müssen, was mindestens drei Minuten in anspruch nehmen würde, und dabei den Haupt-ESP nahezu vollständig blockieren würden, wurde entschieden, den DCF-77 nicht einzubauen.

\chapterauthor{Matthias Unterrainer}

\subsubsection{LCD Display}
\chapterauthor{Matthias Unterrainer}
Das verwendete LCD Display hat eine Anzeige von 20 Zeichen über 4 Zeilen und kann sowohl im 8Bit Modus, als auch im 4Bit Modus betrieben werden.
Es wird mit einer Spannung von 5V versorgt und schaltet sich automatisch nach 1 Minute aus, wenn keine Eingaben durch die Knöpfe erfolgen.
Um Pins zu sparen, wird der 4 Bit Modus genutzt. Dabei werden beim Senden eines Zeichens zunächst die oberen 4 Bit und anschließend die unteren 4 Bit an das Display gesendet. Da jeder Sendevorgang etwa 200 $\mu$s dauert, verdoppelt sich dadurch die Übertragungszeiten. Da der Task über FreeRTOS nicht für derart kurze Zeitspannen inaktiv gesetzt werden kann, mussten diese durch eine Busy-Waiting-Implementierung umgesetzt werden.\\\\
Zusätzlich bietet das LCD Display die Möglichkeit, den Hintergrundkontrast einzustellen. Hierzu wird eine Spannung zwischen 0V und $V_{\text{DD}}$ an den entsprechenden Pin angelegt. Diese Einstellung kann mithilfe des am Steuerbrett, zwischen den Knöpfen, angebrachten Potenziometer vorgenommen werden.\\
Des Weiteren wird die Hintergrundbeleuchtung des Displays ebenfalls vom Neben-ESP gesteuert. Die Versorgungsspannung der Anode des LCD-Display-Moduls ist mit dem GPIO-Pin 13 verbunden, wodurch es zwischen 0V (ausgeschalten) und 3.3V (eingeschalten) umgeschaltet werden kann, und zusammen mit dem Display ein- oder ausgeschalten.

\subsubsection{Knöpfe}
\chapterauthor{Matthias Unterrainer}
Die Knöpfe für das LCD Menu sind über \textit{HIGH} mit dem Neben-ESP verbunden. Für den linken Knopf musste zudem ein externer Pull-Up Widerstand eingebaut werden, da er über den GPIO-Pin 36 läuft, der keine internen Pull-Up/Pull-Down Widerstände hat. Die Knöpfe werden alle 200 $\mu$s abgefragt und können folgende 3 verschiedene Zustände einnehmen:\\
\begin{tabular}{l|c|c}
%\backslashbox{Aktion}{Gedrückte Buttons}    & Button0       & Button1   \\
\hline
NEXT                                        & \checkmark    &           \\
PREV(ious)                                  &               & \checkmark\\
CONF(irm)                                   & \checkmark    & \checkmark\\
\end{tabular}\\
\textit{NEXT} führ dabei zum Vorspringen zum nächste Element im Menü, während \textit{PREV} zum Zurückspringen dient. Ursprünglich wurde \textit{CONF} verwendet um den aktuell angezeigten Wert zu ändern. Nach dem Umzug auf den Neben-ESP war dies jedoch nicht mehr möglich. Nun reinitialisiert \textit{CONF} das LCD Display und lädt die Diplay Konfiguration, die über die Web-Gui eingestellt wird, neu.

\subsection{Algorithmen}
\chapterauthor{Matthias Unterrainer}

\subsubsection{Ausrichtung der Panels}
\input{ausrichtungPanels.tex}

\subsubsection{Nachtabschaltung}
\chapterauthor{Matthias Unterrainer}
Um möglichst viel Energie zu sparen, wurde eine Nachtabschaltung implementiert. Diese führt dazu, das in er Zeit von einer Stunde nach dem Sonnenuntergang bis eine Stunde vor dem Sonnenaufgang, die Solarpanele in eine vorher über die Web-GUI festgelegte Position eingestellt werden, der Task zur ausrichtung der Panele blockiert und ein globales Event \textit{Nachtabschaltung} gesetzt wird, wodurch auch andere Task von der Nachtabschaltung informiert werden.

% Die Berechnung für die Sonnenauf/untergangszeiten basieren auf diesem, ursprünglich vom Nautical Almanac Office veröffentlichen Algorithmus, \cite{nachabschaltung_algo}. Dieser benötigt lediglich den aktuellen Längen-/Breitengrad und das aktuelle Datum, Monat und Tag. 
% Dazu wird zuerst vom Datum, also Monat und Tag, der aktuelle Tag des Jahres berechnet, d.h. der 1.1 ist Tag 1 und der 15.4 ist Tag 74. Dannach wird der Längengrad in Stunden umgerechnet und 

\subsubsection{Akkuladegerät}\label{Akkuladegerät}
\chapterauthor{Lukas Eigenstetter}
Der Algorithmus des Akkuladegerätes kann durch die State Machine in \autoref{stmAkkulader} beschrieben werden.
\begin{figure}[htpb] % {H}
    \centering
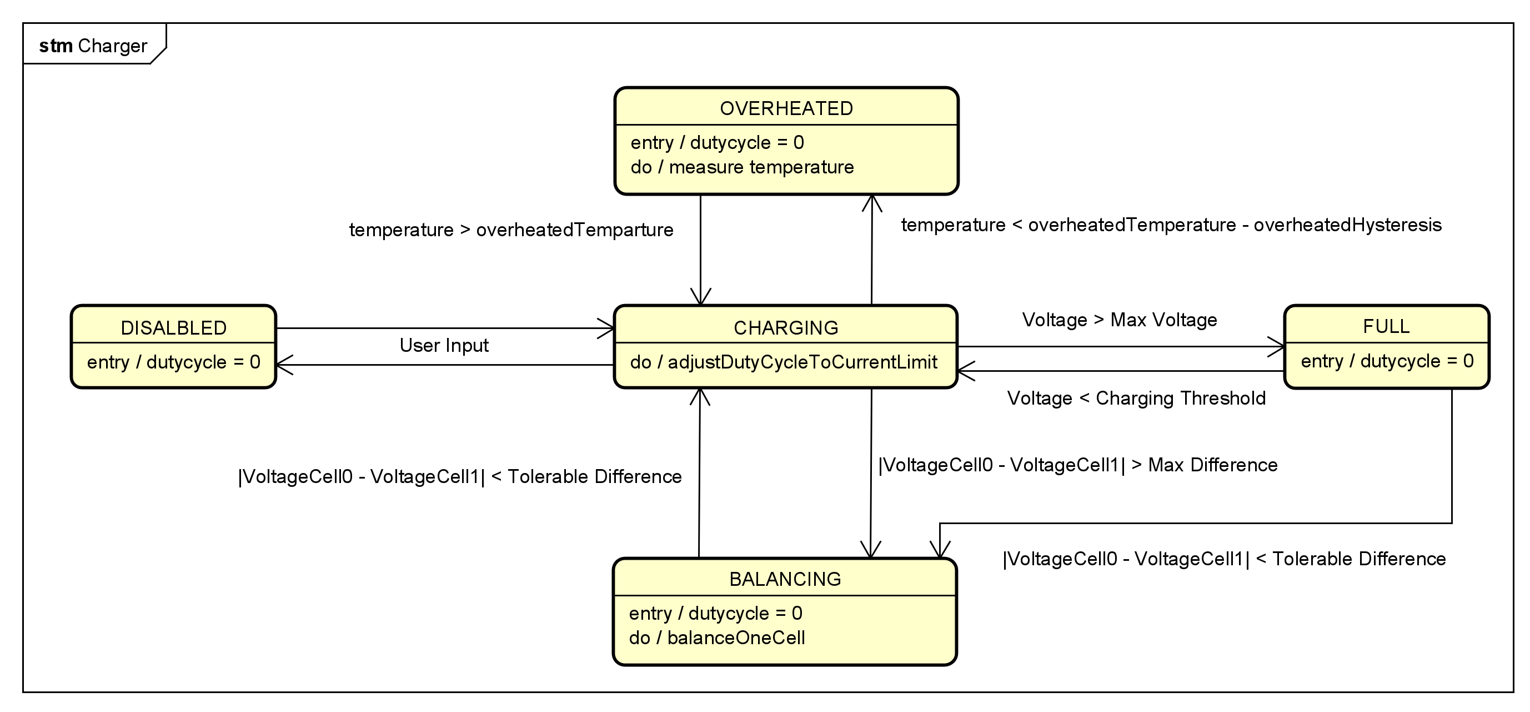
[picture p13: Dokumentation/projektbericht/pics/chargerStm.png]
    
    \caption{State Chart zum Ladealgorithmus}
    \label{stmAkkulader}
\end{figure}
Der zentrale Zustand ist der Zustand \emph{CHARGING}.
In diesem wird das PWM, dessen Schaltung in \autoref{akkuCircuit} beschrieben ist, angepasst.
In allen anderen Zuständen ist der Duty Cycle 0.
Das Ladegerät kann durch den Nutzer im Frontend gestartet oder gestoppt werden.
Im Zustand \emph{CHARGING} wird zusätzlich der Temperatursensor geprüft.
Falls die Temperatur über einem festgelegten Wert liegt, so wird der Zustand \emph{OVERHEATED} angenommen.
Dies dient zum Schutz der Batterie vor zu hohen Temperaturen.  \autocite[S. 53]{chargerBuch}
Falls die Batterie eine gewisse Spannung überschreitet, nimmt das Ladegerät den Zustand \emph{FULL} ein.
So kann ein Laden bis zu einer gewissen Grenze ermöglicht werden.
Im Zustand \emph{BALANCING} wird die vollere der beiden Zellen über einen Widerstand entladen.
Eine detaillierte Beschreibung der Notwendigkeit dieses Verfahrens ist im \autoref{akkuCircuit} beschrieben.
Um häufiges Wechseln zwischen den Zuständen zu vermeiden, sind jeweils Hysteresen definiert.\\
Eine Abschaltung des Systems bei zu niedrigem Ladestand wurde nicht eingebaut, da dies eine relativ schwierige Aufgabe ist.
Um zu messen, ob eine Spannung unterschritten wird, muss das System eingeschaltet sein.
Sinnvoll wäre daher eine analoge Lösung.
Diese könnte durch einen Transistor realisiert werden, der anhand eines Spannungsteilers gesteuert wird.
Das Problem bei dieser Lösung ist, dass die Schaltung nicht im Betrieb konfiguriert werden könnte.
Bei Betrieb mit NiMH Batterien würde dies dazu führen, dass der Ausschaltvorgang an einer falschen Stelle eintritt.\\

Der Ladestrom wird über ein 13 Bit PWM Signal geregelt.
Das Signal wird jeweils um die Differenz des zuletzt gemessenen Stromes in mA und dem derzeitigen PWM Wert angepasst:
$$ PWM_{neu} = PWM_{alt} + (I_{Ziel} - I_{Charger}) \cdot PWM\_REGULATION\_FACTOR $$
Der Wert Reglerkonstante $ PWM\_REGULATION\_FACTOR $ ist 1.\\
Der Zielwert des Ladestroms kann durch den Nutzer mithilfe des Wertes \emph{currentTarget} vorgegeben werden.
Dieser wird bis zum Spannungswert \emph{trickleThreshold} verwendet.
Ab dem Spannungswert \emph{trickleThreshold} wird der Ladestrom $ I_{Ziel} $ linear verringert, bis er bei der \emph{maximumVoltage} auf 0 reduziert wurde.
Abbildung \autoref{ladekurve} zeigt den daraus resultierenden Verlauf für die Standardwerte.
\begin{figure}[htpb] % {H}
    \begin{center}
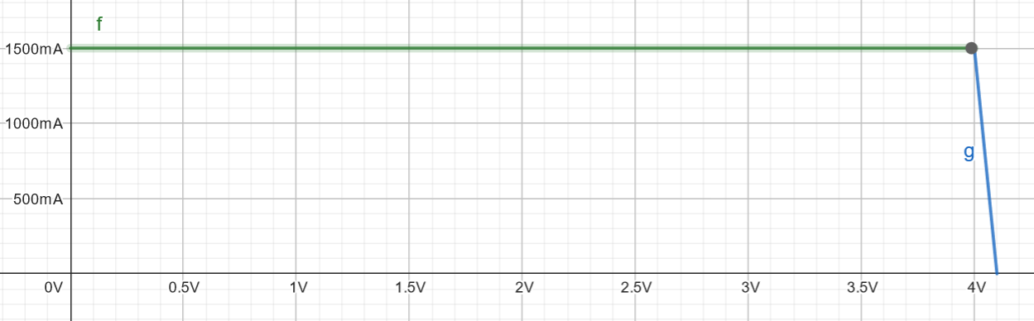
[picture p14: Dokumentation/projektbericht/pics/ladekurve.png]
        
        \caption{Verlauf maximalen Ladestroms in Abhängigkeit der Zellenspannung}\label{ladekurve}
    \end{center}
    Die Darstellung zeigt den Verlauf für die Defaultwerte.
    Die Spannung ist immer pro Zelle zu betrachten.
\end{figure}

Die Gerade im Trickle-Bereich wird durch die folgende Gleichung beschrieben:
$$ I_{target} = I_{currentTarget} + I_{currentTarget} \cdot \frac{U_{trickleOffset}} {U_{trickleThreshold} - U_{maximumVoltage}} $$
Die Werte  $ U_{maximumVoltage} $, $ I_{currentTarget} $ und $ U_{trickleThreshold} $ können durch den Nutzer vorgegeben werden.
$ U_{trickleOffset} $ gibt an, an welcher Stelle des Trickle-Bereichs die Spannung gerade liegt.
Sie wird durch die folgende Gleichung bestimmt:
$$ U_{trickleOffset} = (U_{Battery} - U_{trickleThreshold} \cdot CELL\_COUNT) / CELL\_COUNT $$
Die Anzahl der Akkuzellen, $ CELL\_COUNT $, ist 2.
Professionelle Ladegeräte verwenden meist nicht-lineare Zielströme im Trickle-Bereich. \autocite[S. 50f]{chargerBuch}

\subsubsection{Ladezustandsabschätzung}\label{Ladezustandsabschätzung}
\chapterauthor{Lukas Eigenstetter}
Akkus haben die Eigenschaft, dass sie mit abnehmendem Ladezustand an Spannung verlieren.
Diesen Effekt kann man zur Abschätzung des Ladezustands (State of Charge Estimation) nutzen.
Ein einfaches Verfahren der Ladezustandsabschätzung kann die zuletzt gemessene Spannung der Batterie verwenden.
Da die Spannung der Zellen unter Last um bis zu 600 mV abnimmt, wird eine zusätzliche Metrik benötigt.\\
Diese wird durch die Messungen des Coulomb-Counters umgesetzt.
Durch ein- und abfließenden Strom kann auf die Veränderung des Ladezustands geschlussfolgert werden.
Die Strommessungen bieten jedoch keine Einsicht in den absoluten Ladezustand.
Daher wird ein hybrides Verfahren der Ladezustandsabschätzung umgesetzt, das beide Metriken verwendet:\\
Alle zehn Minuten wird der spannungsbasierte Kalibrierungstask aufgerufen.
In diesem werden High-Power-Circuit und Ladegerät ausgeschaltet, um einen möglichst geringen Strom im System zu haben.
Dann wird eine Millisekunde gewartet und die ADC werden ausgelesen.
Anhand eines separat bestimmten, nicht gemittelten Wertes der Batteriespannung wird durch einen Lookup in einer Wertetabelle der Ladezustand in Prozent bestimmt.
\autoref{socTable} zeigt die hierfür verwendete Tabelle.\\
\begin{figure}[htpb] % {H}
    \centering
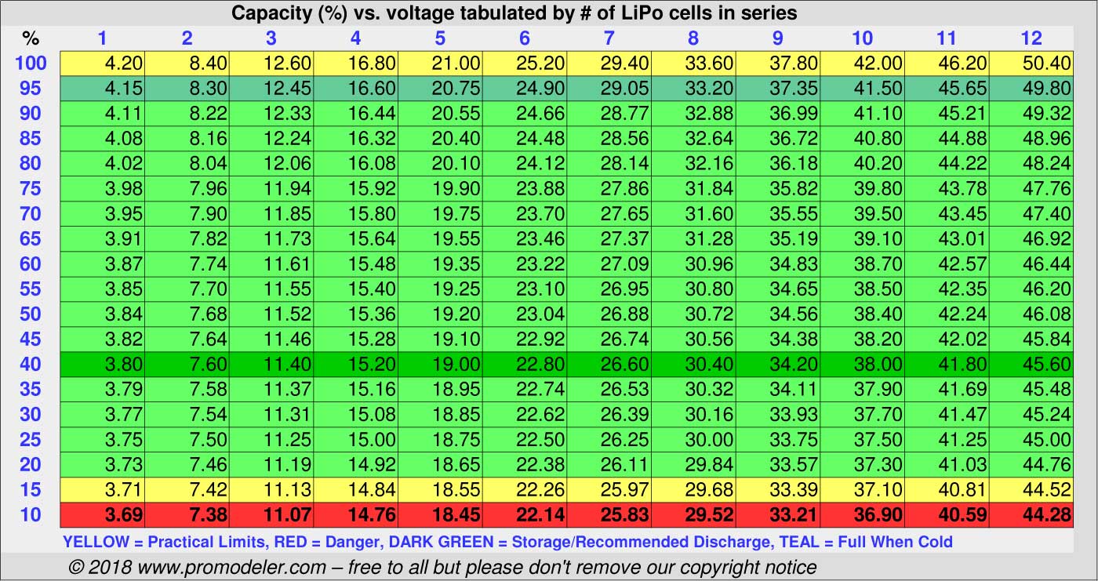
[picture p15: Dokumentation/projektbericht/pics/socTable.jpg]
    
    \caption{Verwendete Tabelle für die Ladezustandsabschätzung \cite{socTable}}
    \label{socTable}
\end{figure}
Zu dieser wurde eine Umkehrfunktion bestimmt, um eine Abbildung von Spannung auf Ladezustandswerte zu erlauben.
Die Tabelle hat 100 Werte und erstreckt sich über den Spannungsbereich von 8.4 V bis 7.4 V.
Die Auflösung ist demnach teilweise höher als in der Tabelle.
In diesen Fällen wurde linear interpoliert.
Die Werte sind liegen im Programm als konstantes Array vor.
Durch die folgende Formel wird der Ladezustand aus der Spannung bestimmt mithilfe eines einzigen Zugriffs bestimmt:
$$ SoC = F_{SoC}((U_{Battery} - 7400) / 10) $$
$F_{SoC}$ ist hierbei die Wertetabelle und $U_{Battery}$ die Batteriespannung in Millivolt.
Im C-Code muss zusätzlich darauf geachtet werden, dass die Spannung im Bereich von 7.4 bis 8.4 V liegt.
Der Task, der für das Auslesen der ADC verantwortlich ist, verändert den Wert des Ladezustands anhand des produzierten und verbrauchten Stroms gemäß der folgenden Formel:\\
$$ SoC = SoC + \frac{Q_{CC} * 10}{K_{Bat}} $$ %TODO prüfen!!
$ Q_{CC} $ ist die gemessene Ladung in Coulomb und $ K_{Bat} $ ist die Kapazität des Akkus in Milliamperestunden.

In der Praxis ist der Stromverbrauch im Ruhezustand bereits hoch genug, um die Spannung der verwendeten Akkus signifikant zu verringern.
Die Kalibrierung liefert deutlich zu niedrige Werte.
Durch die Verwendung eines sparsameren Controllers für das Ladegerät und der Abschaltung aller Module könnte dieses Problem gelöst werden.\\
Da jedoch noch Bugs in Coulomb-Counter-Anpassung existieren, ist der gemessene Ladezustand immer 0. \autocite[S. 139 - 158]{chargerBuch}
\newpage
\section{Verbesserungsmöglichkeiten}
\chapterauthor{Lukas Eigenstetter}
Dieses Kapitel befasst sich mit den Verbesserungsmöglichkeiten im Projekt.
Die bei der Abnahme noch bestehenden Probleme der Teilkomponenten wurden bereits in den jeweiligen Unterkapiteln in \autoref{Dokumentation} beschreiben.
Außerdem werden einige Alternativen aufgezeigt, die zu einem besseren Ergebnis geführt hätten.

\subsection{Planung und Ablauf}
\chapterauthor{Lukas Eigenstetter}
Ein großes Problem in diesem Projekt war die Zeitplanung.
Die Phase der Integration wurde unterschätzt und entsprechend zu spät begonnen.
Bei der Zusammensetzung der Komponenten kamen viele Bugs zum Vorschein und neue Probleme traten auf.
Diese hätten meist durch Unit Tests, Schnittstellentests und frühere Komponenten erkannt werden können.
Außerdem wurde vergessen, die PINs für das SD-Card Modul zu vermerken, wodurch der Neben-ESP erst notwendig wurde.
Diese Fehler und Versäumnisse spiegeln sich in der hohen Stundenzahl ab Woche 13 wider.

% Lukas & Matthias
% kabeldämpfung, smt circuit designen usw...

\subsection{Mechanischer Aufbau}
\chapterauthor{Philipp Thaler, Felix Wagner und Lukas Eigenstetter}
Durch das Verwenden der dickeren Holzplatte für den Oberbau und die dünnere Holzplatte für den Unterbau ergiebt sich ein Balance Problem für den unteren Servomotor.
Dieser benötigt daher mehr Kraft, um die Holzplatte zu rotieren. Daraus ist vermutlich der Verschleiß der Servohörner herzuleiten, der während der Testphase angefallen ist.
Am Ende des Projekts wurde versucht, stabilere Servohebel zu verwenden.
Ein Aluminiumhebel hat noch weniger ausgehalten als der Kunststoffhebel.
\autoref{horn} zeigt ein selbst geschweißtes Horn aus einer Mutter und einer Metallplatte.
Auch dieser Versuch ist fehlgeschlagen.

\begin{figure}[htpb] % {H}
	\begin{center}
	
	\caption{Selbst geschweißter Servohebel (Lukas Eigenstetter)}
	\label{horn}
	\end{center}
	Eine Mutter wurde an eine Metallplatte geschweißt und zugeschliffen.
	Durch ein Einschlagen von Zähnen mithilfe eines Torx-Bit wurde versucht, einen festen Halt zu garantieren.
\end{figure}

Ein Federmechanismus hätte hier etwas Kraft nehmen können, um den Verschleiß geringer zu halten.

Auch Linearlager für das Drehen der Solarplatten führt zu einer geringeren Belastung des oberen Servomotors.
Es wird sich jedoch bewusst gegen den Einsatz entschieden, da die Reibung zwischen dem Holz Stabilität bei den jeweiligen Anschlagpunkten gewährleistet.
Hier haben die Servomotoren am wenigsten Kraft um entgegenzuhalten.

Die Servomotoren haben einige Probleme verursacht. 
Die Anfangs gewählten Modelcraft ES-05 hatten durch ihre mangelhafte Dokumentation für großen Aufwand beim Suchen der korrekten Ansteuerung geführt.
Jedoch erwiesen sich diese Motoren für den Aufbau als zu schwach. 
Somit musste auf die L530MG ausgewichen werden, welche jedoch nur einen Aktionsbereich von 120° gegenüber den 180° der ES-05 bieten. \\
Generell sollte ein anderer Typ von Servomotoren verwendet werden. Die aktuell genutzten Motoren schaffen keine wirkliche Drehung von 180°. Hier könnten Linearaktuatoren verwendet werden.

Eine gute Alternative zu den Servomotoren wären Steppermotoren gewesen. 
Diese hätten sich ebenfalls mit definierten Schritten mit ausreichender Genauigkeit positionieren lassen können.
Die günstigste Option hätte womöglich eine Kombination aus Linearmotor für die Rotation und Servomotor für die Kippfunktion geboten. 
Hierbei würde das Kippen der Solarpanele analog zum aktuellen Aufbau funktionieren. 
Die Rotation würde über den nicht positionierbaren Linearmotor müsste über einen, auf der Rotationsplattform platzierten, Kompasssensor überwacht werden. 
Dabei muss zusätzlich auch auf mögliche Kabelverdrehungen geachtet werden, da beliebig weite Drehungen möglich sind.
\subsection{Sensoren}
\chapterauthor{Johannes Treske}
Die eingebauten Sensoren, vor allem der GPS Sensor, benötigen viel Strom.
Wenn das SunStorage Produkt in Serie gehen würde, sollte man die Überlegung anstellen die verbauten Sensoren zu reduzieren.
Eine Möglichkeit wäre es GPS Modul, Kompass und Beschleunigungssensor wegzulassen.
Da Solaranlagen normalerweise für mehrere Jahrzehnte stationär an einem Ort installiert werden, ist es sinnvoll die GPS-Koordinaten einmal, z.B. über das Webinterface, manuell einzutragen.
Der Kompass kann dadurch überflüssig gemacht werden, dass das komplette System beim Installieren vor Ort korrekt ausgerichtet wird.
Der Beschleunigungssensor wird im SunStorage Projekt dafür verwendet, eine Schieflage des Systems auszugleichen.
In einem realen Szenario ist dieser Ausgleich kaum relevant, solange die Schieflage nicht signifikant ist.
Bei der Installation des Systems kann bereits darauf geachtet werden, dass das System möglichst gerade steht.
Durch das Einsparen der Sensoren kann sowohl Strom als auch Geld gespart werden.

%\subsection{Ein Unterkapitel, das sich der ganzen FreeRTOS und Espressif Kacke beschäftigt, die nicht funktioniert hat und wie man das evtl besser hätte lösen können}

% interner temperatursensor: lukas
\subsection{Sender-Empfänger Setup}\label{KommunikationVerbesserung}
\chapterauthor{Lukas Eigenstetter}
Der Aufbau mit zwei Controllern war anfangs nicht vorgesehen.
Daher wurde eine möglichst unkomplizierte Lösung umgesetzt, die nicht sehr sauber ist.\\
Eine saubere Lösung könnte aus einem kleinen Controller zur Ladesteuerung und für essenzielle Bestandteile und einem großen Controller für Frontend und Module bestehen.\\
Ein ATmega328 hätte genug PINs und ADC, um das Ladesteuergerät zu realisieren.
Dieser hat einen geringeren Stromverbrauch als der ESP-32.
Ein ESP-32 dient dann als Interface für die Module und zum Hosting des Webservers.
Der ATmega328 müsste dauerhaft eingeschaltet sein, während der ESP-32 nur periodisch zum speichern der Datenbank und zum Stellen der Servos benötigt wird.
Der Systemzustand könnte dann im EEPROM des ATmega328 liegen.
Das Starten des Webservers könnte dann über einen physischen Knopf erfolgen.
Nach einem bestimmten Zeitraum ohne Aktion, könnte der Webserver heruntergefahren werden.\\
Alle Bestandteile mit Ausnahme des ATmega328 würden dann über den Buck-Converter versorgt werden.
Der kleine Controller kann durch Setzen des PINs am Buck-Converter die restlichen Bestandteile starten.
Diese Lösung hätte einen deutlich geringeren Stromverbrauch als die ursprünglich geplante Ein-Controller Lösung.\\
Sie verlangt, dass eine bidirektionale Kommunikation zwischen den beiden Controllern möglich ist.
Dafür müsste ein Protokoll und Flusskontrolle umgesetzt werden.
Da auch hier nur Zustandsnachrichten ausgetauscht werden müssen, die eine feste Größe besitzen, wäre eine implizite Flusskontrolle möglich.
Es ist es nicht notwendig, den kompletten Zustand auszutauschen.
Der zweite Controller muss nur die Einstellungen für das Ladegerät empfangen und die zu speichernden Daten senden.
In einer sauberen Lösung würde der Systemzustand nur die Zustandsinformationen enthalten und nicht die Steuerungsinformationen für den zweiten Controller.
Damit wären Haupt-Controller-Zustand, Lade-Controller-Zustand, Haupt-Controller-Nachrichten und Lade-Controller-Nachrichten getrennt.
Im jetzigen Aufbau liegt alles in einer großen State-JSON.\\
Ein weiteres Problem der Umsetzung ist, dass keine Fehlererkennung eingesetzt wird.
Die fehlerfreie Übertragung der Zustandsnachricht könnte durch eine CRC oder eine Prüfsumme gesichert werden.\\
Eine weitere Verbesserung wäre, das Ladegerät als SMT-PCB aufzubauen.
Damit wären die Abweichungen die Verlustleistung geringer.
Dies hätte schon sehr früh im Projektverlauf gemacht werden müssen, da die Lieferzeit eines PCB mehrere Wochen beträgt.
Außerdem sind Korrekturen bei einem Fehler in der Schaltung nur schwer möglich.

\subsection{Timing und Delays}
\chapterauthor{Johannes Treske}
Bei einer Weiterentwicklung des SunStorage Projektes, sollten die Delays der einzelnen Tasks weiter optimiert werden.
Eine Überlegung wäre es, nicht mehr auf ein präventives Schedulingverfahren zu setzen, sondern den Tasks fest zugewiesene Rechenslots zuzuweisen, in denen sie genau einen Durchlauf vollführen.
Dies ist möglich, da die Zeit, die ein Task braucht, um einem Durchlauf zu absolvieren, recht gut zu bestimmen ist und keine besonders zeitkritischen Tasks im Projekt vorhanden sind.
Der Vorteil dabei ist es, dass der Task der gerade ausgeführt wird ohne Unterbrechung seine Aufgabe erledigen kann.
Das bedeutet auch, dass sich Tasks nicht mehr um die Nutzung einer Ressource streiten müssten.

%\subsection{DCF-77}
% matthias: sehr wichtig!1!!elf11!!1

%\subsection{Frontend}
% evtl schiefe ebene in sim einbauen
% anordnungen der displayelemente ermöglichen (Konzept, wie das im gui aussehen könnte)
% weitere mögliche verschönerungen, falls dir noch welche einfallen: Valentin
%Valentin: mehrere Aufrufe für lange Historien

% bessere trennung der informationen, v.a. modulabschaltungen in extra file, state usw... Lukas, Philipp

\newpage
\pagenumbering{Roman}
\listoffigures

\newpage
\listoftables

\newpage
\printbibliography

Alle Links wurden am Abgabetag überprüft.

\end{document}

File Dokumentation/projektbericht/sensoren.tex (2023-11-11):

\subsubsection{GPS}
\chapterauthor{Johannes Treske}
Als GPS Modul haben wir das Modell GT-U7 von Goouuu Tech gewählt.
Dieses Modul kommuniziert über UART und sendet Nachrichten nach NMEA 0183 Standard.
In regelmäßigen Abständen sendet das GPS Modul die NMEA Sätze GGA, GLL, GSA, RMC, VTG und GSV.
Im Recommended Minimum Sentence C (RMC) sind fast alle für uns relevanten Informationen enthalten.
Dieser Satz gibt unter anderem Auskunft über das Datum und die Uhrzeit in UTC, sowie den Längen- und Breitengrad.
Der RMC Satz wird im Folgenden dargestellt:

\begin{center}
    \$GPRMC,HHMMSS,A,BBBB.BBBB,b,LLLLL.LLLL,l,GG.G,RR.R,DDMMYY,M.M,m,F*PP
\end{center}

Jeder NMEA Satz beginnt mit einem Dollarzeichen gefolgt von der Art des Satzes, im Beispiel RMC.
Alle weiteren Werte des Satzes werden durch ein Komma getrennt angegeben.
Ein Satz endet mit einem Asterisk gefolgt von zwei Byte Prüfsumme.
Diese Prüfsumme wird durch eine XOR Verknüpfung aller Nutzbytes berechnet.

Um das GPS Modul komfortabel nutzen zu können, werden Funktionen zum Auslesen von NMEA Sätzen, sowie zum Parsen der Sätze benötigt.

\begin{lstlisting}[language=C]
esp_err_t gpsReceiveNmea(char** nmea, size_t* len);
esp_err_t gpsParseNmea(char* nmea, size_t len, nmea_data_t* nmeaData, nmea_data_type_t* nmeaDataType);
\end{lstlisting}

Mit der \textit{gpsReceiveNmea} Funktion kann stets der nächste vollständige im Buffer gespeicherte NMEA ausgelesen werden.
Der Anfang eines Satzes wird durch das Dollarzeichen bestimmt, das Ende wird bei einem \glqq \textbackslash n\grqq\ erkannt.
Der aus dieser Funktion erhaltene Satz kann mit der Funktion \textit{gpsParseNmea} geparst werden.
Beim Parsen wird die Prüfsumme überprüft und falls diese korrekt ist, werden je nach Art des Satzes die einzelnen Werte des Satzes geparst.
Ist das Parsen erfolgreich, wird ein Objekt mit allen Werten, sowie die Art des NMEAs zurückgegeben.
Um einen bestimmten NMEA Satz zu erhalten, können diese beiden Funktionen in einer Schleife so lange aufgerufen werden, bis der gewünschte Satz gelesen wird.

\subsubsection{I2C-Sensoren}
\chapterauthor{Johannes Treske}
Im SunStorage Projekt werden neben dem GPS Sensor noch drei weitere Sensoren verwendet.
Der Beschleunigungssensor, der Temperatursensor und der Kompass werden über I2C angesprochen.
Das ESP-IDF Framework stellt bereits grundlegende Funktionen zur Kommunikation über I2C zur Verfügung.
Darauf aufbauend wurden Funktionen zum erleichterten Auslesen bzw. Schreiben von Registern der Sensoren geschrieben.
Diese können dann von den von uns geschriebenen Sensortreibern verwendet werden.
Die Treiber wurden hauptsächlich mithilfe der jeweiligen Datenblätter geschrieben.

\paragraph{Gyroskop/Beschleunigungssensor}
\chapterauthor{Johannes Treske}
Das Gyroskop bzw. der Beschleunigungssensor ist ein Modul, das mehrere Messwerte liefert.
Bei diesem Modul werden lediglich die Beschleunigungswerte verwendet, um die Schiefstellung des gesamten Systems zu ermitteln.
Der Treiber für dieses Modul umfasst Funktionen zum Initialisieren, Zurücksetzen, Schlafen legen, Auslesen der Messwerte und Einstellen der Messgenauigkeit.
Die Beschleunigungswerte werden auf drei Achsen gemessen und in G (also ungefähr $9.81\,\frac{m}{s^2}$) ausgegeben.

\paragraph{Barometer/Temperatursensor}
\chapterauthor{Johannes Treske}
Mit dem Barometer kann sowohl der Luftdruck als auch die Temperatur gemessen werden.
Im Projekt wird dieser Sensor verwendet, um die Temperatur der Batterie zu überwachen.
Der Treiber für diesen Sensor bietet die Möglichkeit Druck und Temperatur aus dem Sensor auszulesen, inklusive der Umrechnung der Rohdaten mithilfe der Kalibrierungsregister.
Die Kalibrierungsregister werden beim Initialisieren des Moduls ausgelesen und gespeichert.
Der Sensor gibt Druckwerte in Pascal und Temperaturwerte in Grad Celsius aus.

\paragraph{Kompass}
\chapterauthor{Johannes Treske und Felix Wagner}
Der Kompass bietet die Möglichkeit, die Ausrichtung des Systems zu berechnen.
Der Treiber für den Kompass gibt lediglich die Rohwerte der drei Achsen zurück.
Zur Berechnung der tatsächlichen Werte ist es notwendig, eine statische Kalibrierung vorzunehmen.
Eine Komponente der Kompassachse wird immer dann maximal, wenn die Achse nach Norden zeigt.\\

Die Kalibrierung wird wie folgt vorgenommen.
Die Sensoren, welche die Werte für die drei Achsen des Kompasses bestimmen, müssen zuerst auf ihre Maximal- und Minimalwerte überprüft werden.
Platziert man die ausgegebenen Werte der x- und y-Achse auf einem x-y-Koordinatensystem als Messpunkte, so bilden diese einen Kreis.
\begin{figure}[htpb] % {H}
    \centering
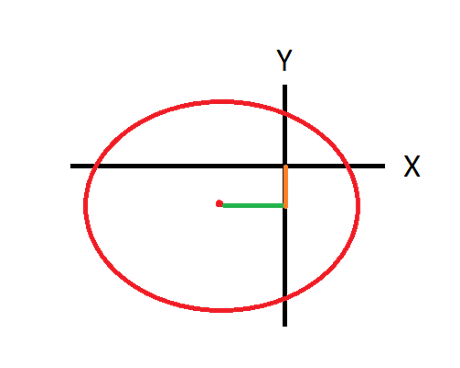
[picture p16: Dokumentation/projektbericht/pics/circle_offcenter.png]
    
    \caption{Kreis nicht im Ursprung}
    \label{fig:circle_offcenter}
\end{figure}
Um jeden Messpunkt zu erhalten, muss der Sensor einmal um alle Achsen gedreht werden.
Der entstehende Kreis ist ohne Kalibrierung nicht zentral im Koordinatensystem platziert.
Ziel ist es, den Kreis in den Koordinatenursprung zu verschieben.
\autoref{fig:circle_offcenter} zeigt nicht kalibrierten Zustand und \autoref{fig:circlecenter} den korrekt verschobenen Kreis.
\begin{figure}[htpb] % {H}
    \centering
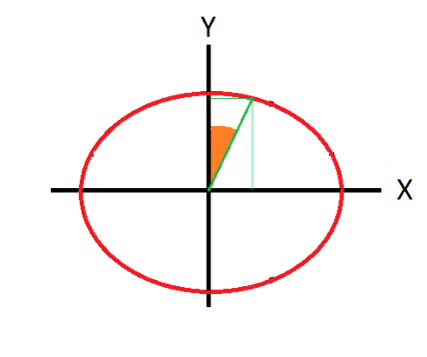
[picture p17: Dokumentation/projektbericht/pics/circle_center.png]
    
    \caption{Kreis im Ursprung}
    \label{fig:circlecenter}
\end{figure}

Für die Kalibrierung werden die Kompasswerte im Programmcode mehrmals pro Sekunde abgefragt und in Variablen gespeichert.
Dabei gibt es für jede Achse einen Minimal- und Maximalwert.
Nachdem der Kompass um alle drei Achsen gedreht wurde, sind die sechs Werte erfasst.
Anschließend muss daraus der jeweilige Korrekturfaktor für die einzelnen Achsen abgeleitet werden.
Ziel ist es, den Minimal- und Maximalwert für die Berechnung der Nordausrichtung im gleichen Abstand links und rechts des Koordinatenursprungs zu setzen, wie in \autoref{fig:circle_offcenter} gezeigt.
Dabei werden pro Achse die Maximalwerte und die Minimalwerte addiert und diese Summe halbiert.
Nun hat man die nötigen Korrekturfaktoren für die Kalibrierung und kann diese mit den x-, y- und z-Werte verrechnen.
Eine Eigenschaft des QMC5883L-Kompassmodul ist, dass dieses nicht ständig neu kalibriert werden muss.

\subsubsection{Servomotoren}
\chapterauthor{Felix Wagner}
Bei den Servomotoren handelt es sich um Analogservos der Firma Bluebird mit der Bezeichnung BMS-L530MG.
Diese benötigen eine Spannung von 4.5 V bis 6.5 V werden über ein PWM-Signal gesteuert.
Dieses Steuersignal hat eine Frequenz von 250 Hz und stellt den Servomotor bei einem Dutycycle von 1330 µs in seine mittlere Stellung.
Gegen den Uhrzeigersinn kann mit einem Dutycycle von 900 µs auf 60° gestellt werden.
Gleichfalls kann mit dem Dutycycle 2100 µs der Aktionsradius im Uhrzeigersinn gefahren werden.
Damit ergibt sich ein Gesamtaktionsbereich von 120°. \autocite{servomotor}

\paragraph{Ansteuerung}
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

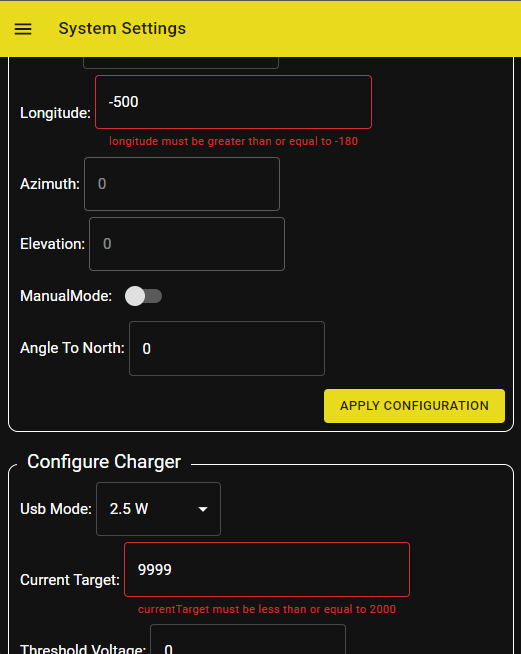
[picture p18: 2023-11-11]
Dokumentation/projektbericht/pics/Screenshot_SystemSettings.png

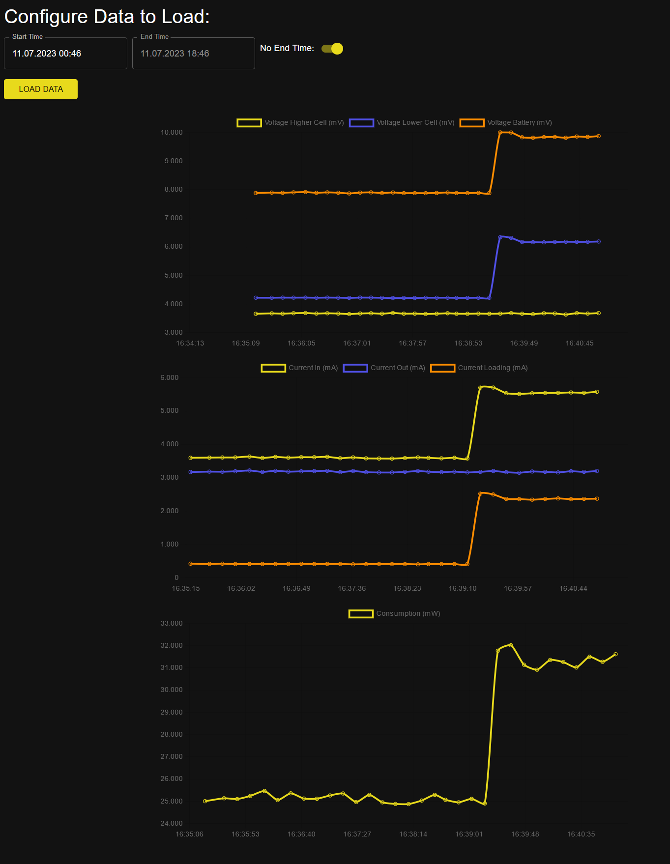
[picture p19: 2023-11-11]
Dokumentation/projektbericht/pics/beispielplot.png

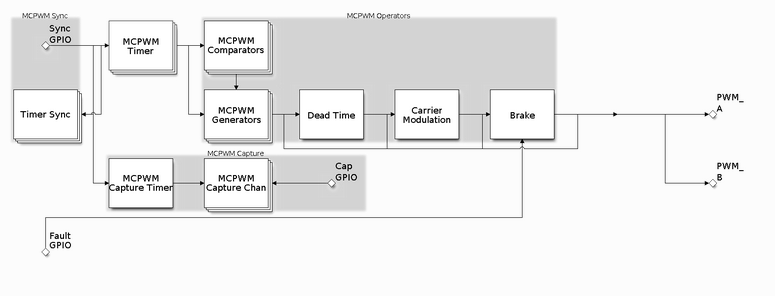
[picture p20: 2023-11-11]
Dokumentation/projektbericht/pics/mcpwmOverview.png

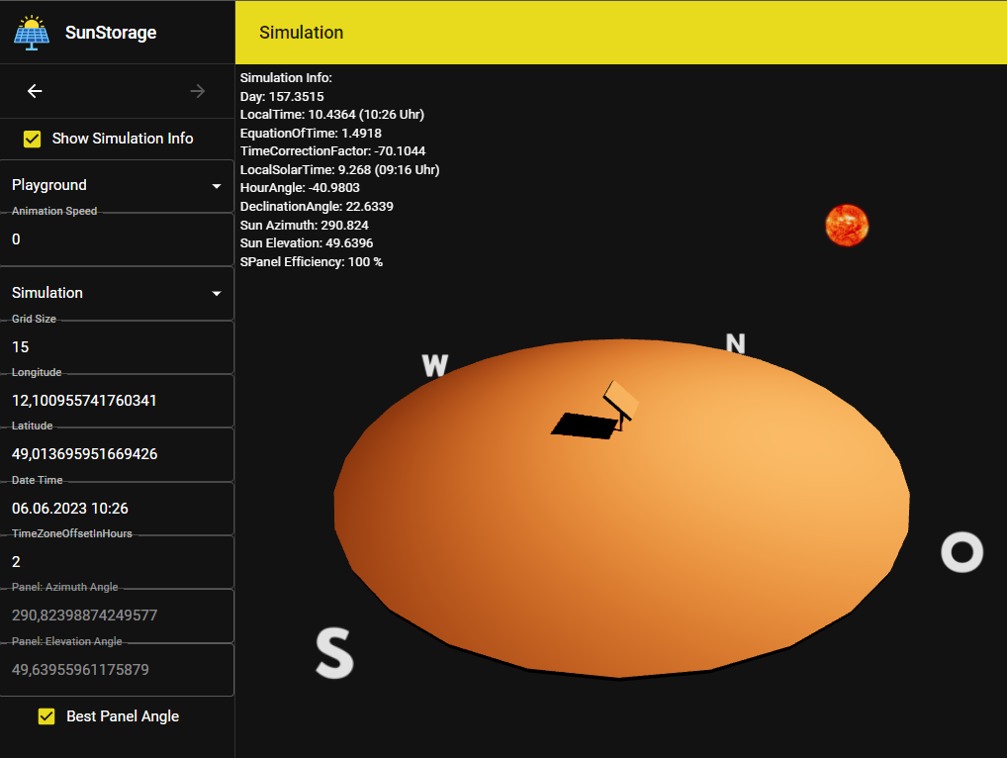
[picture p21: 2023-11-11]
Dokumentation/projektbericht/pics/Screenshot_WebUI_Simulation.png

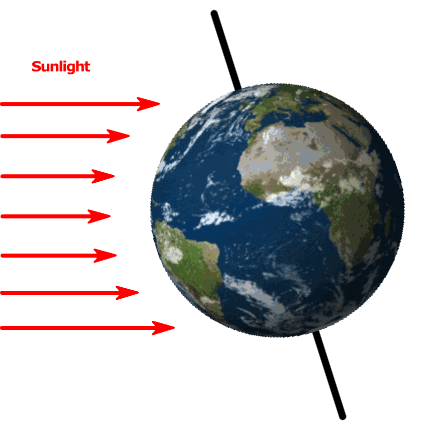
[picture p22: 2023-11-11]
Dokumentation/projektbericht/pics/erde_sonne_angle.png

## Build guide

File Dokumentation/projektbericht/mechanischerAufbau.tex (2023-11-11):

\subsubsection{Mechanischer Aufbau}
\chapterauthor{Philipp Thaler}
%Philipp, Matthias und Lukas

In diesem Abschnitt wird auf den mechanischen Aufbau des Systems eingegangen.

\begin{figure}[htpb] % {H}
    \centering
    
    \caption{Aufbau des Systems}\label{aufbauSeitenansicht}
\end{figure}

\autoref{aufbauSeitenansicht} zeigt die Holzkonstruktion mit den beiden Servomotoren und den Solarmodulen.

Die beiden Solarplatten sind auf Holzlatten festgeschraubt. 
Um eine Drehung von 180° zu ermöglichen, sind die Holzlatten auf einem Holzstab befestigt.
Dieser wird von den beiden Stützhölzern links und rechts gehalten. 
Der Servomotor, der für die Neigung der Solarmodule verantwortlich ist, sitzt auf einer eigenen Stütze, wie im Hintergrund von \autoref{aufbauLagerung} zu erkennen.

Eine Schwierigkeit ist, den Servomotor mit der Stange auf dem die Module gelagert sind, zu verbinden.
Hierzu wird der Hebel des Servomotors an ein Holzquadrat geschraubt, welches ebenso an dem Holzstab befestigt ist.
Vor dem Anbringen muss der Motor in eine der beiden Nullstellungen gebracht werden.
Die Solarmodule werden um 90° zur Bodenplatte geneigt, um eine Nullstellung als Ausgangspunkt zu erhalten. 
Somit ist es dem oberen Servomotor möglich, die Solarmodule um 90° in beide Richtungen zu neigen.

\begin{figure}[htpb] % {H}
    \centering
    
    \caption{Lagerung der oberen Konstruktion}\label{aufbauLagerung}
\end{figure}

\autoref{aufbauLagerung} zeigt, wie die obere Konstruktion mit der unteren Holzkonstruktion verbunden ist.
In der Mitte ist das verwendete Kugellager zu erkennen. 
Dieses ist durch vier Schrauben mit der oberen Platte verbunden und ermöglicht dem unteren Servomotor den gesamten Oberbau um 180° zu drehen.

Hierbei ist die Schwierigkeit den unteren Servomotor mit der oberen Platte zu verbinden. 
Dazu wird in die obere Platte der Unterkonstruktion ein Loch in der Mitte ausgeschnitten, um den Servohebel an die Bodenplatte der Oberkonstruktion anzubringen.
Nun kann der untere Servomotor mit den vier langen Schrauben und einem Holzeinsatz unten an den Servohebel gepresst werden. 
Um nicht zu viel Druck auf den Servomotor auszuüben, sind Gegenmuttern angebracht.

In \autoref{aufbauLagerung} ist zu erkennen, wie die Kabeldurchführung der Solarmodule und des oberen Servomotors gehandhabt wird. 
Hierzu wird ein etwa 1 cm dicker Halbkreisbogen ausgeschnitten. 
Somit können sich die Kabel auch bei der Rotation der Basis frei bewegen und behindern die Rotation nicht.

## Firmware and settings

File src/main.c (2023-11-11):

#include <esp_log.h>
#include <esp_system.h>
#include <freertos/FreeRTOS.h>
#include <freertos/task.h>

#include "globalInit.h"

#ifdef TX
#include "tasks/adcReadTask.h"
#include "tasks/batteryChargerTask.h"
#include "tasks/compasscaliTask.h"
#include "tasks/dcf77Task.h"
#include "tasks/displayTask.h"
#include "tasks/socCalibrationTask.h"
#include "tasks/statsCalcTask.h"
#include "tasks/storeReadingsTask.h"
#include "tasks/sunAlignTask.h"
#include "tasks/testTasks.h"
#include "tasks/usbChargerTask.h"
#include "tasks/writeSystemStateTask.h"
#endif

#include "tasks/espCommTask.h"

#ifdef RX
#include "tasks/displayButtonsTask.h"
#include "tasks/displayTask.h"
#include "tasks/panelAlignTask.h"
#endif

void app_main() {
    esp_log_level_set("*", ESP_LOG_NONE);
    // uncomment one of these tasks to test a specific module comment out everything else
    // xTaskCreate(HelloWorldTestTask, "Hello_World_Test_Task", 1024, NULL, tskIDLE_PRIORITY, NULL);
    // xTaskCreate(compassTestTask, "Compass_Test_Task", 1024 * 10, NULL, tskIDLE_PRIORITY, NULL);
    // xTaskCreate(gyroscopeTestTask, "Gyroscope_Test_Task", 1024 * 10, NULL, tskIDLE_PRIORITY, NULL);
    // xTaskCreate(gpsTestTask, "GPS_Test_Task", 1024 * 10, NULL, tskIDLE_PRIORITY, NULL);
    // xTaskCreate(databaseTestTask, "Database_Test_Task", 1024 * 100, NULL, tskIDLE_PRIORITY, NULL);
    // xTaskCreate(barometerTestTask, "Barometer_Test_Task", 1024 * 10, NULL, tskIDLE_PRIORITY, NULL);
    // xTaskCreate(nightShutdownTask, "Night Shutdown Task", 1024, NULL, tskIDLE_PRIORITY, NULL);
    // xTaskCreate(chargerPwmTask, "PWM Task", 10240, NULL, 2, NULL);
    // xTaskCreate(usbChargerTask, "USB Task", 10240, NULL, 1, NULL);
    // xTaskCreate(adcTask, "ADC Task", 10240, NULL, tskIDLE_PRIORITY, NULL);
    // xTaskCreate(persistSystemStateTask, "Persist System State Task", 10240, NULL, tskIDLE_PRIORITY, NULL);
    // xTaskCreate(readCoulombCounterTestTask, "stats_calc", 1024 * 4, NULL, tskIDLE_PRIORITY, NULL);
    // xTaskCreate(sunTrackingTask, "sunTrackingTask", 10240, NULL, tskIDLE_PRIORITY, NULL);
    // xTaskCreate(readCoulombCounterTestTask, "readCoulombCounterTestTask", 1024 * 100, NULL, tskIDLE_PRIORITY, NULL);

    // initialize all modules
    if (globalInit() != ESP_OK) {
        ESP_LOGE("app_main", "critical module failed to initialize. restarting....");
        esp_restart();
    }

// TODO create application tasks with xTaskCreate MAX_NAME_LENGTH 16 Bytes
#ifdef TX
    ESP_LOGI("main", "THIS IS A SENDER");
    xTaskCreate(adcReadTask, "adc_read", 1024 * 5, NULL, tskIDLE_PRIORITY, NULL);
    xTaskCreate(batteryChargerTask, "battery_charger", 1024 * 3, NULL, tskIDLE_PRIORITY, NULL);
    xTaskCreate(socCalibrationTask, "soc_calibration", 1024 * 5, NULL, tskIDLE_PRIORITY, NULL);
    xTaskCreate(storeReadingsTask, "store_readings", 1024 * 10, NULL, 1, NULL);
    xTaskCreate(sunAlignTask, "sun_align", 1024 * 5, NULL, tskIDLE_PRIORITY, NULL);
    xTaskCreate(usbChargerTask, "usb_charger", 1024 * 10, NULL, tskIDLE_PRIORITY, NULL);
    xTaskCreate(writeSystemStateTask, "write_state", 1024 * 4, NULL, tskIDLE_PRIORITY, NULL);
    xTaskCreate(statsCalcTask, "stats_calc", 1024 * 4, NULL, tskIDLE_PRIORITY, NULL);
    // xTaskCreate(compasscaliTask, "compasscaliTask", 1024 * 5, NULL, tskIDLE_PRIORITY, NULL);
    // xTaskCreate(dcf77Task, "dcf77", 1024 * 2, NULL, tskIDLE_PRIORITY, NULL);
#endif

#ifdef RX
    ESP_LOGI("main", "THIS IS A RECEIVER");
    xTaskCreate(displayTask, "display", 1024 * 10, NULL, tskIDLE_PRIORITY, &displayButtonsNotificationHandle);
    xTaskCreate(displayButtonsTask, "display_buttons", 1024 * 10, NULL, tskIDLE_PRIORITY, NULL);
    xTaskCreate(espCommReceiveTask, "esp_receive", 1024 * 10, NULL, tskIDLE_PRIORITY, NULL);
    xTaskCreate(panelAlignTask, "panelAlignTask", 1024 * 5, NULL, tskIDLE_PRIORITY, NULL);

#endif
    return;
}

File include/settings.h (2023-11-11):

#ifndef SETTINGS_H
#define SETTINGS_H

#include <stdbool.h>

typedef enum {
    DISABLED,
    CHARGING,
    FULL,
    BALANCING,
    OVERHEATED
} CHARGER_MODE;

typedef enum {
    _2_POINT_5_WATT,
    _5_WATT,
    _10_WATT
} USB_MODE;

#define NUM_DISPLAY_ITEMS 35

typedef struct {
    bool itemEnabled[NUM_DISPLAY_ITEMS];
} display_config_t;

extern const char* DISPLAY_NAMES[NUM_DISPLAY_ITEMS];

/*================== TASK SETTINGS ===================*/

#define STORE_READINGS_TASK_DELAY ((uint32_t)10000 / portTICK_PERIOD_MS)
#define STATE_WRITE_DELAY ((uint32_t)3000 / portTICK_PERIOD_MS)
#define USB_CHARGER_DELAY ((uint32_t)5000 / portTICK_PERIOD_MS)
#define SOC_TASK_DELAY ((uint32_t)60000000 / portTICK_PERIOD_MS)
#define BATTERY_CHARGER_TASK_DELAY ((uint32_t)3000 / portTICK_PERIOD_MS)
#define ADC_TASK_DELAY ((uint32_t)100 / portTICK_PERIOD_MS)
#define ESP_COMM_RECEIVE_TASK_DELAY ((uint32_t)500 / portTICK_PERIOD_MS)

#define STORE_READINGS_TASK_MAX_GPS_READS 10

/*====================================================*/

/*=================== MISC ===========================*/
#define xSemaphorePoll(semaphore) xSemaphoreTake(semaphore, 1000 / portTICK_PERIOD_MS)

#define ESP_HANDLE_ERR(error, msg) \
    if (error != ESP_OK) {         \
        ESP_LOGE("", msg);         \
        return error;              \
    }

/*====================================================*/

/*=================== I2C SETTINGS ===================*/

#define I2C_MASTER_PORT I2C_NUM_0
#define I2C_MASTER_SDA_IO GPIO_NUM_21
#define I2C_MASTER_SCL_IO GPIO_NUM_22
#define I2C_MASTER_FREQ_HZ 100000
#define I2C_MS_TO_WAIT 5000

/*====================================================*/

/*================== COMPASS MODULE ==================*/

#define COMPASS_MODULE_ADDR 0x0D  // 7 bit address of GY-271
#define CM_MODE_STANDBY 0x00
#define CM_MODE_CONTINUOUS_MEASUREMENT 0x01

// axis output registers
#define CM_DOXL 0x00
#define CM_DOXH 0x01
#define CM_DOYL 0x02
#define CM_DOYH 0x03
#define CM_DOZL 0x04
#define CM_DOZH 0x05

#define CM_SR 0x06  // status register

// temperature output registers
#define CM_TOL 0x07
#define CM_TOH 0x08

// control registers
#define CM_CR0 0x09
#define CM_CR1 0x0A

#define CM_FBR 0x0B  // SET/RESET period

#define CM_UPDATE_DATA_RATE 0b00      // 0b00 -> 10Hz; 0b01 -> 50Hz; 0b10 -> 100Hz; 0b11 -> 200Hz
#define CM_MAGNETIC_FIELD_RANGE 0b00  // 0b00 -> 2G; 0b01 -> 8G
#define CM_OVER_SAMPLE_RATIO 0b00     // 0b00 -> 512; 0b01 -> 256; 0b10 -> 128; 0b11 -> 64
#define CM_ROL_PNT 1                  // enable rolling pointer for continuous data readout
#define CM_INT_DISABLE 1              // disable interrupt on DRDY PIN

/*====================================================*/

/*==================== BAROMETER =====================*/

#define BAROMETER_ADDR 0x77  // 7 bit address of GY-68
#define BMP_POWER_ON_RESET 0xB6
#define BMP_CHIP_ID 0x55

#define BMP_MEAS_CTRL_TEMP 0x2E
#define BMP_MEAS_CTRL_PRES 0x34

// output registers
#define BMP_DOXLSB 0xF8
#define BMP_DOLSB 0xF7
#define BMP_DOMSB 0xF6

#define BMP_CR 0xF4   // control register
#define BMP_RST 0xE0  // reset register
#define BMP_IDR 0xD0  // chip id register

// calibration register
#define BMP_CAL_AC1H 0xAA
#define BMP_CAL_AC1L 0xAB
#define BMP_CAL_AC2H 0xAC
#define BMP_CAL_AC2L 0xAD
#define BMP_CAL_AC3H 0xAE
#define BMP_CAL_AC3L 0xAF
#define BMP_CAL_AC4H 0xB0
#define BMP_CAL_AC4L 0xB1
#define BMP_CAL_AC5H 0xB2
#define BMP_CAL_AC5L 0xB3
#define BMP_CAL_AC6H 0xB4
#define BMP_CAL_AC6L 0xB5
#define BMP_CAL_B1H 0xB6
#define BMP_CAL_B1L 0xB7
#define BMP_CAL_B2H 0xB8
#define BMP_CAL_B2L 0xB9
#define BMP_CAL_MBH 0xBA
#define BMP_CAL_MBL 0xBB
#define BMP_CAL_MCH 0xBC
#define BMP_CAL_MCL 0xBD
#define BMP_CAL_MDH 0xBE
#define BMP_CAL_MDL 0xBF

#define BMP_OVER_SAMPLE_RATIO 0b00     // 0b00 -> ultra low power (single); 0b01 -> standard (2 times); 0b10 -> high resolution (4 times); 0b11 -> ultra high resolution (8 times)
#define BMP_MEASUREMENT_DELAY_US 5000  // OSR = 0b00 -> 5ms; OSR = 0b01 -> 8ms; OSR = 0b10 -> 14ms; OSR = 0b11 -> 26ms;

/*====================================================*/

/*==================== GYROSCOPE =====================*/

#define GYROSCOPE_ADDR_LOW 0x68   // 7 bit address of MPU6050 with address pin low (GND).
#define GYROSCOPE_ADDR_HIGH 0x69  // 7 bit address of MPU6050 with address pin high (VCC).
#define GYROSCOPE_ADDR GYROSCOPE_ADDR_LOW

#define GY_BAND_260_HZ 0
#define GY_BAND_184_HZ 1
#define GY_BAND_94_HZ 2
#define GY_BAND_44_HZ 3
#define GY_BAND_21_HZ 4
#define GY_BAND_10_HZ 5
#define GY_BAND_5_HZ 6

#define GY_GYRO_RANGE_250_DEG 0
#define GY_GYRO_RANGE_500_DEG 1
#define GY_GYRO_RANGE_1000_DEG 2
#define GY_GYRO_RANGE_2000_DEG 3

#define GY_ACCEL_RANGE_2_G 0
#define GY_ACCEL_RANGE_4_G 1
#define GY_ACCEL_RANGE_8_G 2
#define GY_ACCEL_RANGE_16_G 3
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

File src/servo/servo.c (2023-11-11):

#include "servo.h"

#include <esp_log.h>

#include "freertos/FreeRTOS.h"
#include "freertos/task.h"
#include "rom/ets_sys.h"

#define DEBUG

static inline uint32_t angle_to_compare(int angle) {
    return (uint32_t)(angle * 7.38 + 820);  //(2150.0f - 820.0f) / (180) ; with 120° 11.0833
}

mcpwm_cmpr_handle_t comparatorRotate = NULL;
mcpwm_cmpr_handle_t comparatorTilt = NULL;

esp_err_t initServo() {
    esp_err_t error = ESP_OK;
    mcpwm_timer_handle_t timerRotate = NULL;
    mcpwm_timer_config_t timer_configRotate = {
        .group_id = 0,
        .clk_src = MCPWM_TIMER_CLK_SRC_DEFAULT,
        .resolution_hz = 1000000,
        .period_ticks = 4000,
        .count_mode = MCPWM_TIMER_COUNT_MODE_UP,
    };
    mcpwm_new_timer(&timer_configRotate, &timerRotate);
    mcpwm_oper_handle_t operRotate = NULL;
    mcpwm_operator_config_t operator_configRotate = {
        .group_id = 0,
    };
    mcpwm_new_operator(&operator_configRotate, &operRotate);
    mcpwm_operator_connect_timer(operRotate, timerRotate);

    mcpwm_comparator_config_t comparator_configRotate = {
        .flags.update_cmp_on_tez = true,
    };
    mcpwm_new_comparator(operRotate, &comparator_configRotate, &comparatorRotate);
    mcpwm_gen_handle_t genRotate = NULL;
    mcpwm_generator_config_t gen_configRotate = {
        .gen_gpio_num = OUTPUT_MOTOR_ROTATE,
    };
    mcpwm_new_generator(operRotate, &gen_configRotate, &genRotate);
    mcpwm_comparator_set_compare_value(comparatorRotate, angle_to_compare(0));
    mcpwm_generator_set_action_on_timer_event(genRotate, MCPWM_GEN_TIMER_EVENT_ACTION(MCPWM_TIMER_DIRECTION_UP, MCPWM_TIMER_EVENT_EMPTY, MCPWM_GEN_ACTION_HIGH));
    mcpwm_generator_set_action_on_compare_event(genRotate, MCPWM_GEN_COMPARE_EVENT_ACTION(MCPWM_TIMER_DIRECTION_UP, comparatorRotate, MCPWM_GEN_ACTION_LOW));
    mcpwm_timer_enable(timerRotate);
    mcpwm_timer_start_stop(timerRotate, MCPWM_TIMER_START_NO_STOP);

    mcpwm_timer_handle_t timerTilt = NULL;
    mcpwm_timer_config_t timer_configTilt = {
        .group_id = 1,
        .clk_src = MCPWM_TIMER_CLK_SRC_DEFAULT,
        .resolution_hz = 1000000,
        .period_ticks = 4000,
        .count_mode = MCPWM_TIMER_COUNT_MODE_UP,
    };
    mcpwm_new_timer(&timer_configTilt, &timerTilt);
    mcpwm_oper_handle_t operTilt = NULL;
    mcpwm_operator_config_t operator_configTilt = {
        .group_id = 1,
    };
    mcpwm_new_operator(&operator_configTilt, &operTilt);
    mcpwm_operator_connect_timer(operTilt, timerTilt);

    mcpwm_comparator_config_t comparator_configTilt = {
        .flags.update_cmp_on_tez = true,
    };
    mcpwm_new_comparator(operTilt, &comparator_configTilt, &comparatorTilt);
    mcpwm_gen_handle_t genTilt = NULL;
    mcpwm_generator_config_t gen_configTilt = {
        .gen_gpio_num = OUTPUT_MOTOR_TILT,
    };
    mcpwm_new_generator(operTilt, &gen_configTilt, &genTilt);
    mcpwm_comparator_set_compare_value(comparatorTilt, angle_to_compare(0));
    mcpwm_generator_set_action_on_timer_event(genTilt, MCPWM_GEN_TIMER_EVENT_ACTION(MCPWM_TIMER_DIRECTION_UP, MCPWM_TIMER_EVENT_EMPTY, MCPWM_GEN_ACTION_HIGH));
    mcpwm_generator_set_action_on_compare_event(genTilt, MCPWM_GEN_COMPARE_EVENT_ACTION(MCPWM_TIMER_DIRECTION_UP, comparatorRotate, MCPWM_GEN_ACTION_LOW));
    mcpwm_timer_enable(timerTilt);
    mcpwm_timer_start_stop(timerTilt, MCPWM_TIMER_START_NO_STOP);

    return error;
}
uint16_t currDutyRotate = 0;
void setDutyRotate(uint16_t duty) {
    while (currDutyRotate != duty) {
        ((currDutyRotate < duty) ? (currDutyRotate++) : (currDutyRotate--));
        mcpwm_comparator_set_compare_value(comparatorRotate, angle_to_compare(currDutyRotate));
        printf("rotate duty %lu\n", angle_to_compare(currDutyRotate));
        ets_delay_us(DELAY_VALUE * 1000);
    }

    printf("rotate duty: %lu\n", angle_to_compare(currDutyRotate));
}

uint16_t currDutyTilt = 0;
void setDutyTilt(uint16_t duty) {
    while (currDutyTilt != duty) {
        ((currDutyTilt < duty) ? (currDutyTilt++) : (currDutyTilt--));
        mcpwm_comparator_set_compare_value(comparatorTilt, angle_to_compare(currDutyTilt));
        printf("tilt duty %lu\n", angle_to_compare(currDutyTilt));
        ets_delay_us(DELAY_VALUE * 1000);
    }
    printf("Tilt duty: %lu\n", angle_to_compare(currDutyTilt));
}

// for physical setup:
/*
if setup looking north (compass y to north aka heading = 0°)
rotate: 0%   -> horizontal from north to south
        50%  -> horizontal from west to east
        100% -> horizontal from south to north
        0° -> 360°

        in simulation
        0° = north -> 90° = west -> 180° south -> 270° = east

tilt:   0%   -> if rotate 50% then looking south
        50%  -> parallel to baseplate
        100% -> if rotate 50% then looking north
        0° -> 180° or -90° -> +90°
        but simulation makes 0% north and 100% south :(
*/
void setSunpos(int16_t rotateAngle, int16_t tiltAngle) {
    // 0 < all angles < 360°
    if (rotateAngle < 0) {
        int16_t temp = abs(rotateAngle);
        temp %= 360;
        rotateAngle = 360 + -temp;
    } else {
        rotateAngle %= 360;
    }

    if (tiltAngle < 0) {
        int16_t temp = abs(tiltAngle);
        temp %= 360;
        tiltAngle = 360 + -temp;
    } else {
        tiltAngle %= 360;
    }

    // 0 < tilt_angle < 180
    if (tiltAngle > 180 && tiltAngle < 270) {
        tiltAngle = 180;
    }
    if (tiltAngle < 0 || tiltAngle > 270) {
        tiltAngle = 0;
    }

    // translations for 180° servos:
    if (rotateAngle > 180) {
        rotateAngle -= 180;
        tiltAngle = 180 - tiltAngle;
    }

    // translate angle to dutycycle
    // reverse control
    // rotateDuty = DUTY_100_PERCENT - RATIO_DEG_2_PERCENT * rotateAngle;
    // tiltDuty = DUTY_100_PERCENT - RATIO_DEG_2_PERCENT * tiltAngle;
    /*
    for 120° servo



    if (rotateAngle > 150){
        rotateAngle = 120;
    }
    if (rotateAngle < 30){
        rotateAngle = 0;
    }
    if (rotateAngle > 30 && rotateAngle < 150){
        rotateAngle -= 30;
    }
    if(tiltAngle > 150){
        tiltAngle = 120;
    }
    if(tiltAngle < 30){
        tiltAngle = 0;
    }
    if (tiltAngle > 30 && tiltAngle < 150){
        tiltAngle -= 30;
    }
    */

    setDutyRotate(180 - rotateAngle);
    setDutyTilt(tiltAngle);
}
